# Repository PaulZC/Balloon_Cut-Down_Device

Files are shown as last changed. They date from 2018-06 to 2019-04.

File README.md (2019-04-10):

# Balloon_Cut-Down_Device

A cut-down device suitable for use on High Altitude Balloons and other remote actuation projects.



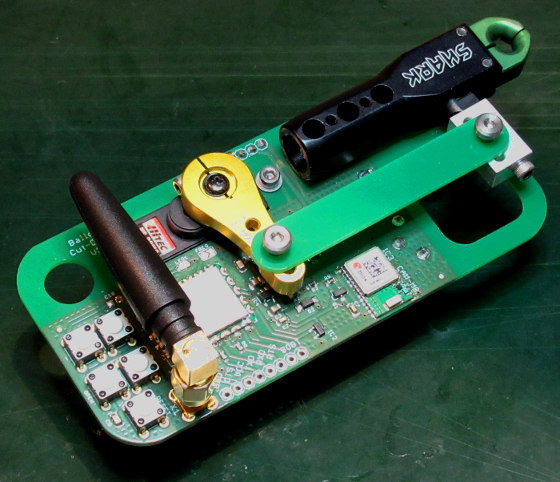
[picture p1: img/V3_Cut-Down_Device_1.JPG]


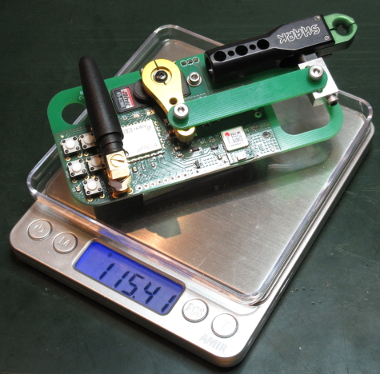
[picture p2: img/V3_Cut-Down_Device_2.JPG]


Designed to be triggered by the [Iridium Beacon Radio Board](https://github.com/PaulZC/Iridium_Beacon_Radio_Board),
carried by the [Iridium 9603N V5 Beacon](https://github.com/PaulZC/Iridium_9603_Beacon), the cut-down will be triggered
when it receives its own (unique) serial number on the chosen radio channel. The number of cut-downs that could be
triggered by a single Iridium Beacon is essentially unlimited. The cut-down can also be configured to trigger at
a pre-defined altitude.

The device comprises:
- [Scott Archery Shark release aid](https://scottarchery.com/collections/releases/products/shark-release), actuated by a
- [HiTec HS-82MG servo](https://www.servoshop.co.uk/index.php?pid=HITHS82MG&area=Servo), controlled by the
- [LPRS eRIC4 or eRIC9 integrated radio module](http://www.lprs.co.uk/products/easyradio-ism-modules/eric-soc-rf-modules.html).
- The altitude is provided by a [u-blox CAM-M8Q GNSS receiver](https://www.u-blox.com/en/product/cam-m8-series)

See [LEARN.md](https://github.com/PaulZC/Balloon_Cut-Down_Device/blob/master/LEARN.md) for further details.

See [SERVO.md](https://github.com/PaulZC/Balloon_Cut-Down_Device/blob/master/SERVO.md) for details on how to modify the HiTec servo for
high altitude operation.

See [SHARK.md](https://github.com/PaulZC/Balloon_Cut-Down_Device/blob/master/SHARK.md) for details on how to incorporate the Scott Archery Shark release aid
into the Cut-Down Device.

See [ASSEMBLY.md](https://github.com/PaulZC/Balloon_Cut-Down_Device/blob/master/ASSEMBLY.md) for details on how to assemble the PCB and the device itself.

See [CONFIGURE.md](https://github.com/PaulZC/Balloon_Cut-Down_Device/blob/master/CONFIGURE.md) for details on how to configure the servo positions and altitude limit.

See [Balloon_Cut-Down_Device.pdf](https://github.com/PaulZC/Balloon_Cut-Down_Device/blob/master/Balloon_Cut-Down_Device.pdf) for the schematic,
layout and Bill Of Materials.

The [Eagle](https://github.com/PaulZC/Balloon_Cut-Down_Device/tree/master/Eagle) directory contains the schematic and pcb design files.

The [eRIC](https://github.com/PaulZC/Balloon_Cut-Down_Device/tree/master/eRIC) directory contains the code for the eRIC integrated radio module.

The [Drawings](https://github.com/PaulZC/Balloon_Cut-Down_Device/tree/master/Drawings) directory contains the drawings for the trigger linkage.

If you have found this project useful and if you are able to, please cite the paper:

P. Clark et al, An open source toolkit for the tracking, termination and recovery of high altitude balloon flights and payloads, 2019 JINST 14 P04003
[DOI:10.1088/1748-0221/14/04/P04003](https://doi.org/10.1088/1748-0221/14/04/P04003)

The Accepted Manuscript is available on arXiv: http://arxiv.org/abs/1904.04321

This project is distributed under a Creative Commons Attribution + Share-alike (BY-SA) licence.
Please refer to section 5 of the licence for the "Disclaimer of Warranties and Limitation of Liability".

Enjoy!

**_Paul_**

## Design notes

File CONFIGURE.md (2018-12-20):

# Balloon Cut-Down Device - Configuration

A cut-down device suitable for use on High Altitude Balloons and other remote actuation projects.







Designed to be triggered by the [Iridium Beacon Radio Board](https://github.com/PaulZC/Iridium_Beacon_Radio_Board),
carried by the [Iridium 9603N V5 Beacon](https://github.com/PaulZC/Iridium_9603_Beacon), the cut-down will be triggered
when it receives its own (unique) serial number on the chosen radio channel. The number of cut-downs that could be
triggered by a single Iridium Beacon is essentially unlimited. The cut-down can also be configured to trigger at
a pre-defined altitude. The altitude is provided by a u-blox CAM-M8Q GNSS receiver.

## Set_Altitude:

There are two methods to set the altitude limit: using the switches; or via a radio message:

### Setting the Altitude Limit using the Switches:

The code enters Set_Altitude mode if the eRIC comes out of reset with the MINUS switch held down:
- Push and hold the MINUS switch;
- then press and release the RESET switch;
- then release the MINUS switch.
- The device will then enter Set_Altitude mode.



The LED will flash three times to show that the digit three is selected.

Pressing the MINUS switch decrements the digit by one.

Pressing the PLUS switch increments the digit by one.

Pressing the CLOSE switch causes the digit to be stored as the altitude limit tens of kilometers.

Pressing the OPEN switch causes the digit to be stored as the altitude limit units of kilometers.

In the animation, the sequence of events is:
- The MINUS switch is pressed and held
- The RESET switch is pressed and released
- The MINUS switch is released
- The cut-down is now in Set_Altitude mode
- The LED flashes three times to show the digit three
- The MINUS switch is pressed and released once
- The LED flashes twice to show the digit two
- The CLOSE switch is pressed and released
- Two is stored in the altitude limit tens of kilometers and the LED gives a long flash
- The MINUS switch is pressed and released once
- The LED flashes once to show the digit one
- The MINUS switch is pressed and released once
- The LED stops flashing to show the digit zero
- The OPEN switch is pressed and released
- Zero is stored in the altitude limit units of kilometers and the LED gives a long flash
- The altitude limit is now 20km
- The RESET switch is pressed and released
- The cut-down goes into normal operation
- The LED flashes twice, followed by a long flash, to indicate the altitude limit is 20km

The eRIC will stay in Set_Altitude mode until reset. Always reset the eRIC to start normal operation.

To disable the altitude limit, set it to 99km. This causes the CAM-M8Q GNSS receiver to be switched completely off,
significantly extending the battery life.

### Setting the Altitude Limit using a Radio Message:

Each eRIC has a unique serial number. The custom code running on the eRIC will set the altitude limit when it receives a data packet containing:
the eRIC serial number; followed by a "2"; followed by two digits which represent the altitude limit is kilometres.

If the serial number of the eRIC is _12345678_, an altitude limit of 33km (33000m) will be set when the eRIC receives:
- _12345678233_

If you are using the [Iridium Beacon](https://github.com/PaulZC/Iridium_9603_Beacon) and the
[Iridium Beacon Radio Board](https://github.com/PaulZC/Iridium_Beacon_Radio_Board) to control the cut-down, you will need to set the altitude limit via a RADIO command.

If you want to set the altitude limit to 33km (33000m), send:
- _[RADIO=12345678233]_

To set the altitude limit to 1km (1000m), send:
- _[RADIO=12345678201]_

The altitude limit can be disabled by setting it to 99km. This causes the CAM-M8Q GNSS receiver to be switched completely off, significantly extending the battery life.
Send:
- _[RADIO=12345678299]_

The altitude limit can be re-enabled by setting it to anything other than 99km.

## Set_Servo:

**It is safest to disconnect the trigger linkage from the servo arm _before_ putting the device into Set_Servo mode. Remove the shoulder screw which connects the
linkage to the servo arm. Replace it after the servo limits have been set and the device has been reset.**

**If you are setting the servo positions for the first time, do not install the servo arm on the servo until the device is in Set_Servo mode and the servo has moved to
its mid-range position.**

The code enters Set_Servo mode if the eRIC comes out of reset with the PLUS switch held down:
- Push and hold the PLUS switch;
- then press and release the RESET switch;
- then release the PLUS switch.
- The device will then enter Set_Servo mode.



The servo is moved to its mid-range position (PWM = 1500). 

Depending on whether the PLUS or MINUS switches are held down, the servo is moved towards one limit (PWM = 900) or the other (PWM = 2100).

With the Shark release closed, hold the trigger linkage over the servo arm and move the servo until the holes are slightly offset as shown.

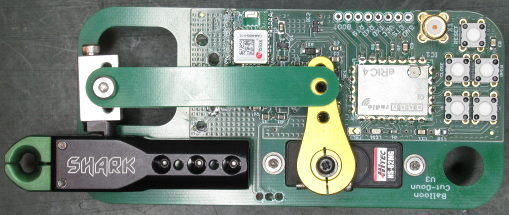
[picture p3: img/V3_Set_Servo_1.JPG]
V3_Set_Servo_1


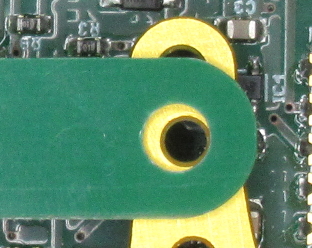
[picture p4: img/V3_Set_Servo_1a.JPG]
V3_Set_Servo_1a


When the CLOSE switch is pressed, the servo position is written into non-volatile memory. The LED will give a long flash while the setting is storted.

Next, open the Shark release and move the servo until the holes are slightly offset as shown.

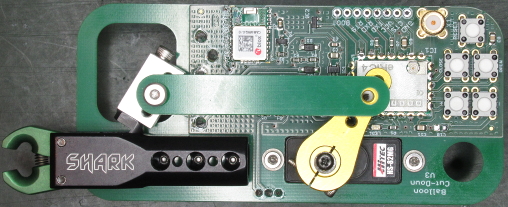
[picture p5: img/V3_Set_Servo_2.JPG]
V3_Set_Servo_2


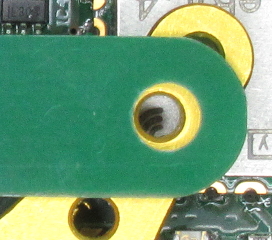
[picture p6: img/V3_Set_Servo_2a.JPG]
V3_Set_Servo_2a


When the OPEN switch is pressed, the servo position is written into non-volatile memory. The LED will give a long flash while the setting is storted.

It is important that the holes are slightly offset as shown, to prevent the servo from attempting to force the released aid open or closed.
This will damage the servo.

The eRIC will stay in this mode until reset.

As the servo is powered continuously in Set_Servo mode, the battery will discharge quickly if the device is left in this mode.
Always reset the device to put it back into Cut_Down mode when the servo positions have been stored.

After resetting the device, the shoulder screw can be replaced and the OPEN and CLOSE switches can be used to move the servo.

## Licence

This project is distributed under a Creative Commons Share-alike 4.0 licence.
Please refer to section 5 of the licence for the "Disclaimer of Warranties and Limitation of Liability".
  
Enjoy!

**_Paul_**

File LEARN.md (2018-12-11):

# Balloon Cut-Down Device

A cut-down device suitable for use on High Altitude Balloons and other remote actuation projects.







Designed to be triggered by the [Iridium Beacon Radio Board](https://github.com/PaulZC/Iridium_Beacon_Radio_Board),
carried by the [Iridium 9603N V5 Beacon](https://github.com/PaulZC/Iridium_9603_Beacon), the cut-down will be triggered
when it receives its own (unique) serial number on the chosen radio channel. The number of cut-downs that could be
triggered by a single Iridium Beacon is essentially unlimited. The cut-down can also be configured to trigger at
a pre-defined altitude. The altitude is provided by a u-blox CAM-M8Q GNSS receiver.

## The Design

See [Balloon_Cut-Down_Device.pdf](https://github.com/PaulZC/Balloon_Cut-Down_Device/blob/master/Balloon_Cut-Down_Device.pdf) for the schematic,
layout and Bill Of Materials.

The [Eagle](https://github.com/PaulZC/Balloon_Cut-Down_Device/tree/master/Eagle) directory contains the schematic and pcb design files.

See [ASSEMBLY.md](https://github.com/PaulZC/Balloon_Cut-Down_Device/blob/master/ASSEMBLY.md) for details on how to assemble the PCB and the device itself.

See [CONFIGURE.md](https://github.com/PaulZC/Balloon_Cut-Down_Device/blob/master/CONFIGURE.md) for details on how to configure the servo positions and altitude limit.

The key components of Balloon Cut-Down Device are:

### Scott Archery Shark Release Aid
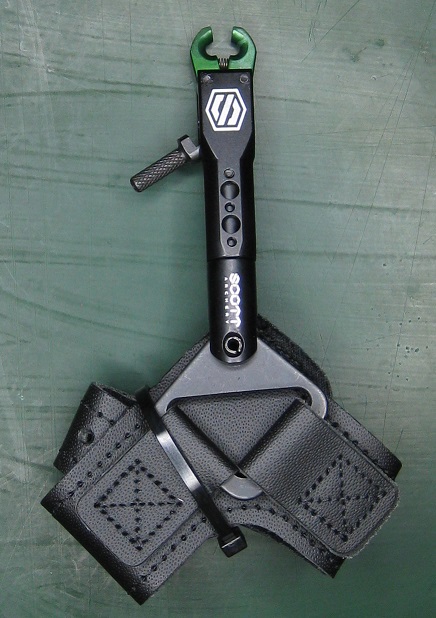
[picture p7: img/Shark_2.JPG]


- [Scott Archery Shark release aid](https://scottarchery.com/collections/releases/products/shark-release)

See [SHARK.md](https://github.com/PaulZC/Balloon_Cut-Down_Device/blob/master/SHARK.md) for details on how to incorporate the Scott Archery Shark release aid
into the Cut-Down Device.

### Hi-Tec HS-82MG Micro Servo
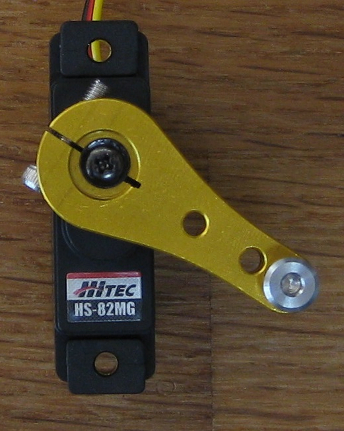
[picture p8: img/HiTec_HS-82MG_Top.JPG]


- [HiTec HS-82MG servo](https://www.servoshop.co.uk/index.php?pid=HITHS82MG&area=Servo)
- with [Tower Pro CH1.0H3G arm](https://www.servoshop.co.uk/index.php?pid=CH10H3G&area=ACCS)

See [SERVO.md](https://github.com/PaulZC/Balloon_Cut-Down_Device/blob/master/SERVO.md) for details on how to modify the HiTec servo for
high altitude operation.

### eRIC integrated controller
The heart of the Cut-Down Device is the eRIC4 or eRIC9 [easyRadio Integrated Controller](http://www.lprs.co.uk/products/easyradio-ism-modules/eric-soc-rf-modules.html).

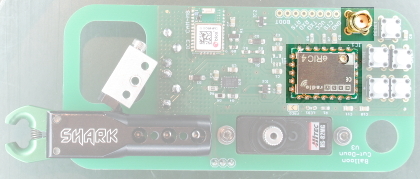
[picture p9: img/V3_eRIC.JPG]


Either an eRIC4 or an eRIC9 can be installed. The eRIC4 operates at 402-470 MHz for Europe, APAC and China. The eRIC9 operates at 804-940 MHz for Europe,
North & South America, India and China. Solder the _FREQ_ split pad to select the eRIC9 915 MHz band.

Each eRIC has a unique serial number. The custom code running on the eRIC will trigger the cut-down when it receives a data packet containing that serial number.

The Shark release will open when the eRIC receives:
- Its serial number
- Or its serial number followed by a "1"

The Shark release will close when the eRIC receives:
- Its serial number followed by a "0"

If the serial number of the eRIC is _12345678_, the Shark will open when the eRIC receives either:
- _12345678_

or
- _123456781_

The Shark will close when the eRIC receives:
- _123456780_

If you are using the [Iridium Beacon](https://github.com/PaulZC/Iridium_9603_Beacon) and the
[Iridium Beacon Radio Board](https://github.com/PaulZC/Iridium_Beacon_Radio_Board) to control the cut-down, you will need to send the commands:
- _[RADIO=12345678]_ or _[RADIO=123456781]_ to open the Shark release
- _[RADIO=123456780]_ to close the Shark release

You can set the altitude limit via radio by sending: the eRIC serial number; followed by a "2"; followed by two digits which represent the altitude limit is kilometres.

If you want to set the altitude limit to 33km (33000m), send:
- _[RADIO=12345678233]_

To set the altitude limit to 1km (1000m), send:
- _[RADIO=12345678201]_

The altitude limit can be disabled by setting it to 99km. This causes the CAM-M8Q GNSS receiver to be switched completely off, significantly extending the battery life.
Send:
- _[RADIO=12345678299]_

The altitude limit can be re-enabled by setting it to anything other than 99km.

### u-blox CAM-M8Q GNSS Receiver
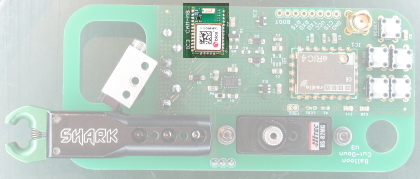
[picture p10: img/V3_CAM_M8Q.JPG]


Altitude data is provided by a u-blox CAM-M8Q GNSS receiver. To save power, the CAM-M8Q is configured to use only GPS satellites and ignores GLONASS, Galileo and BeiDou satellites.
Once the receiver has established a fix, the CAM-M8Q is put into low power mode to further extend the battery life. The CAM-M8Q can be disabled by setting the altitude limit to 99km.

### MCP111T-240 Reset Supervisor
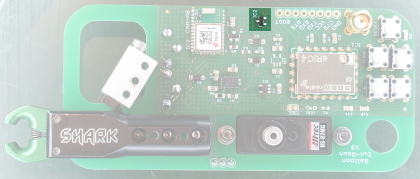
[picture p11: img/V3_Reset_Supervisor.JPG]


The Microchip MCP111-240 has an open drain output which holds the eRIC in reset until the supply rises above 2.4V, ensuring a clean start on power-up.

### SPX3819-3.3 Voltage Regulator
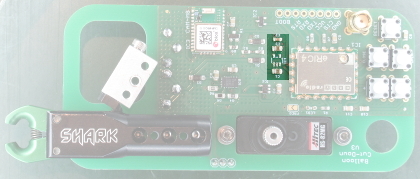
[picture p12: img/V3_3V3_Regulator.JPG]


The SPX3819-3.3 Voltage Regulator regulates the output from the battery, or the USB port, providing 3.3V for the eRIC and the CAM-M8Q.

MBR120 diodes protect the USB port and the battery from each other.

### MPM3610 Voltage Regulator
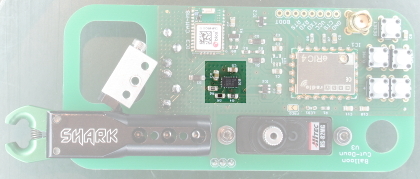
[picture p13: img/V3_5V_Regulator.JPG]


The MPM3610 Voltage Regulator regulates the output from the battery, providing 5V for the servo. The servo will only operate when a battery is connected, it
won't work when the device is powered from USB alone.

### 74AHCT1G125 Level Shifter
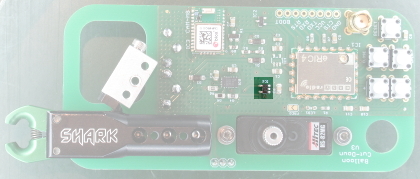
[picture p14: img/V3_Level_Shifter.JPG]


The 74AHCT1G125 Level Shifter is a non-inverting buffer which converts the 3.3V Pulse Width Modulation pulses from the eRIC to 5V for the servo.

### Switches
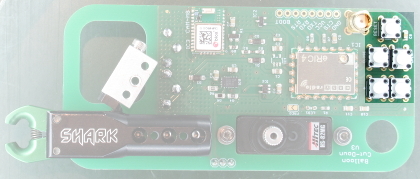
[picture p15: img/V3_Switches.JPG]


The cut-down device has five switches:
- CLOSE
- OPEN
- PLUS (+)
- MINUS (-)
- RESET

Press and release RESET to reset the eRIC.

Pressing OPEN will cause the servo to move the Shark trigger to the open position.

Pressing CLOSE will cause the servo to move the Shark trigger to the closed position.

The PLUS and MINUS switches are used to put the device into [Set_Servo](https://github.com/PaulZC/Balloon_Cut-Down_Device/blob/master/CONFIGURE.md#set_servo)
or [Set_Altitude](https://github.com/PaulZC/Balloon_Cut-Down_Device/blob/master/CONFIGURE.md#set_altitude) mode at reset.

### I/O Pins
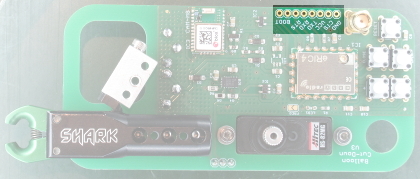
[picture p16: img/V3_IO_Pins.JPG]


The eight input/output pins are used to configure the eRIC. See [Configure the eRIC](https://github.com/PaulZC/Balloon_Cut-Down_Device/blob/master/ASSEMBLY.md#configure-the-eric)
for more details.

### Servo Pins
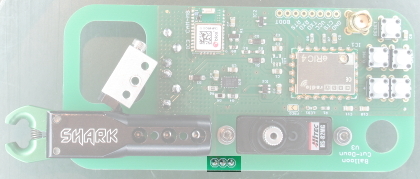
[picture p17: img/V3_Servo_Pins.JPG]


Connect the Hi-Tec HS-82MG Micro Servo to the PCB using standard 0.1" header strip (three-way) (e.g. Farnell 1593425)

## How much does the device weigh?

Including an Energiser® Ultimate Lithium L522 (PP3) battery, it weighs 115g.

V3_Cut-Down_Device_2

## What fasteners do I need?

To secure the servo to the base plate:
- M2.5 x 14 Hex Drive Screw x 2 (McMaster 91292A017)
- M2.5 Nylon-Insert Locknut x 2 (McMaster 93625A102)
- M2.5 Washer x 2 (McMaster 90965A115)

To secure the Shark release to the base plate:
- 4-40 UNC x ¼" Socket Head Screw x 3 (McMaster 92196A106)

To secure the trigger block to the Shark trigger:
- 4-40 UNC x ¾" Socket Head Screw (McMaster 92196A113)

To secure the trigger linkage to the trigger block and Tower Pro arm:
- M3 x 4mm Dia x 4mm Long Shoulder Screw x 2 (McMaster 90323A211)

## Antenna

Recommended antenna for the eRIC4 is:
- LPRS ANT-SR433 (Farnell part 2096221)

Recommended antenna for the eRIC9 is:
- LPRS ANT-SR900 (Farnell part 2096219)

http://www.lprs.co.uk/products/antennas-cables-connectors/stubby-antennas.html

The horizontal antenna orientation is important if the cut-down is positioned directly above the Iridium Beacon Radio Board on the balloon cord.

## Which 9V battery should I use?

Energiser® Ultimate Lithium L522 (PP3)

## Will this really work at altitude?

Yes. I have tested the device at -47C using dry ice. The servo moved slower than usual at that temperature, but it did release as expected.
The device was powered by an Energiser® Ultimate Lithium L522 (PP3) battery. A standard 9V battery won't work at that temperature.

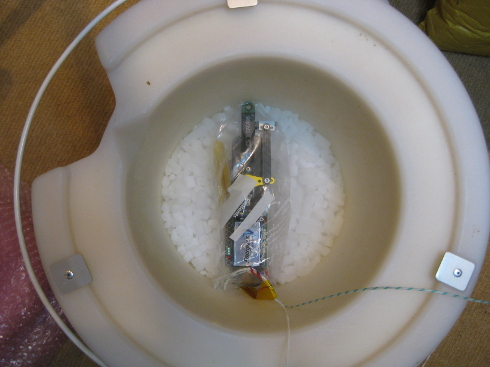
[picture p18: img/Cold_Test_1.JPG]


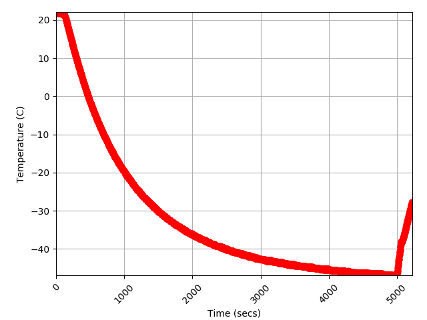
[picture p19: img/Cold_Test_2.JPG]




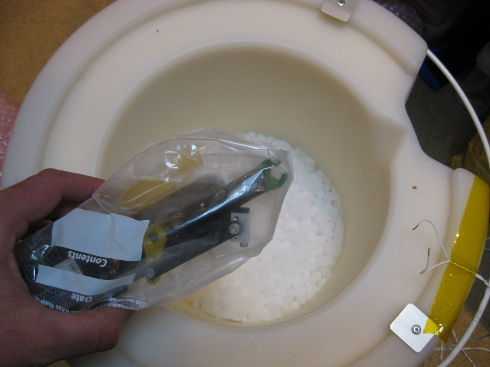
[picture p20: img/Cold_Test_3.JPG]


## Do you recommend coating the board once it is populated?

As a minimum, I'd recommend applying a coat of acrylic protective lacquer to the processor and surrounding components (especially the crystal).
If you're using an aerosol, be careful to mask off the connectors and switches first.

## How do I set the servo positions and altitude limit?

See [CONFIGURE.md](https://github.com/PaulZC/Balloon_Cut-Down_Device/blob/master/CONFIGURE.md) for details on how to configure the servo positions and altitude limit.

## The LED flashes when I connect the battery or reset the eRIC. Why?

When the battery is connected or the reset switch is pressed, the cut-down goes into normal operation. The LED flashes to indicate the altitude limit. The default is
33km so the LED will flash three times, pause, then flash three times again.

A zero is indicated by a long flash. Two flashes followed by a long flash indicates an altitude limit of 20km.
A long flash followed by one flash indicates a limit of 1km.

To test that the CAM-M8Q is operating correctly, try setting an altitude limit of 0km (indicated by two long flashes).
The Shark will open as soon as a GPS signal is acquired (unless you are below sea level!).

## Acknowledgements

This project wouldn't have been possible without the open source designs and code kindly provided by:

### LPRS
- http://www.lprs.co.uk/products/easyradio-ism-modules/eric-soc-rf-modules.html
- http://www.lprs.co.uk/assets/files/eRIC4_9_Datasheet_1.34.pdf
- http://www.lprs.co.uk/assets/files/Custom%20programming%20eRIC.zip
- http://www.lprs.co.uk/knowledge-centre/code-examples.html

### Alan Carvalho de Assis
- https://github.com/acassis/tinygps

### Mikal Hart
- https://github.com/mikalhart/TinyGPS

## Licence

This project is distributed under a Creative Commons Share-alike 4.0 licence.
Please refer to section 5 of the licence for the "Disclaimer of Warranties and Limitation of Liability".

Enjoy!

**_Paul_**

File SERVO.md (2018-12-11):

# Servo Modification

The Balloon Cut-Down Device uses a [HiTec HS-82MG servo](https://www.servoshop.co.uk/index.php?pid=HITHS82MG&area=Servo) to operate the
[Scott Archery Shark release aid](https://scottarchery.com/collections/releases/products/shark-release). These servos are lightweight and provide high torque
for their size. But, to allow them to operate reliably at high altitude (low pressure) and low temperature, the standard grease inside the servo needs to be
replaced and lacquer needs to be applied to the internal circuit board.

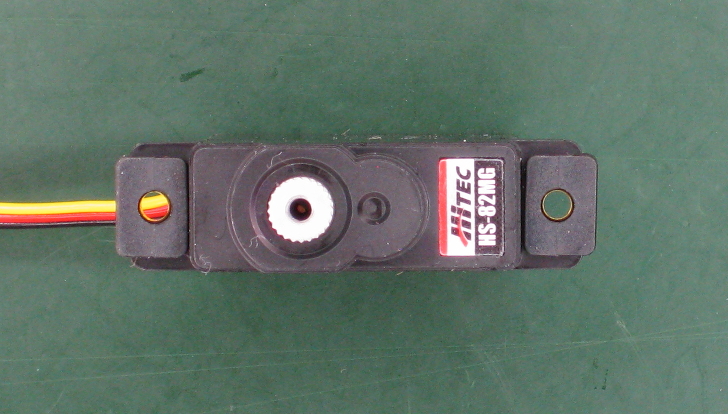
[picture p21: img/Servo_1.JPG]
Servo_1


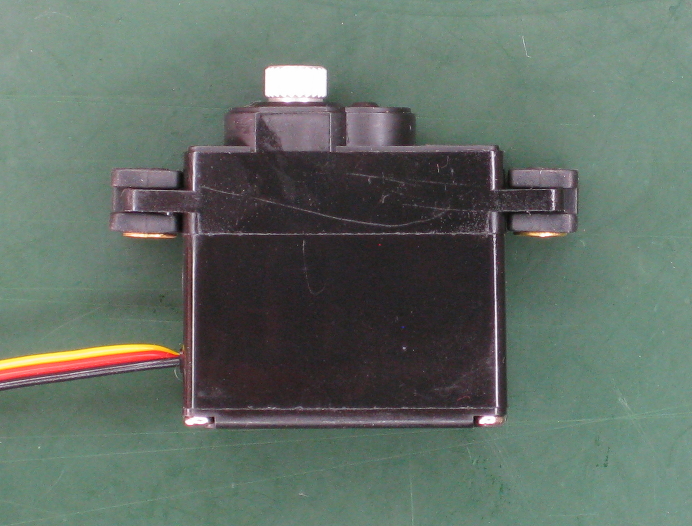
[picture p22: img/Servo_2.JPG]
Servo_2


### Set the Servo to Mid-Range

When you connect the servo to a freshly-programmed cut-down device circuit board and press either the Open or the Close button, the circuit board will
move the servo to its mid-range position. The servo position is set by a Pulse Width Modulation (PWM) signal on the yellow wire. A pulse width of 1.5msec
(1500usec) repeating every 20msec (50Hz) will set the servo to mid-range. It is important you do this as it will help you relocate the half-moon output gear
in the correct position.

You can see how the PWM pulse width causes the servo position to change in the following three images:

- Pulse Width 900usec (0.9msec)

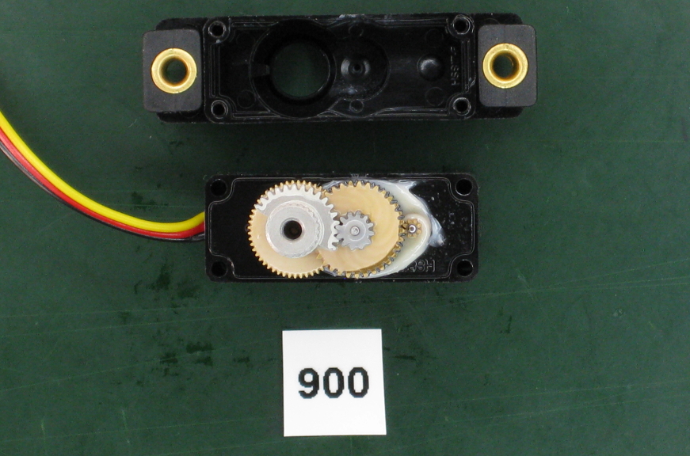
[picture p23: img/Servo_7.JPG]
Servo_7


- Pulse Width 1500usec (1.5msec)

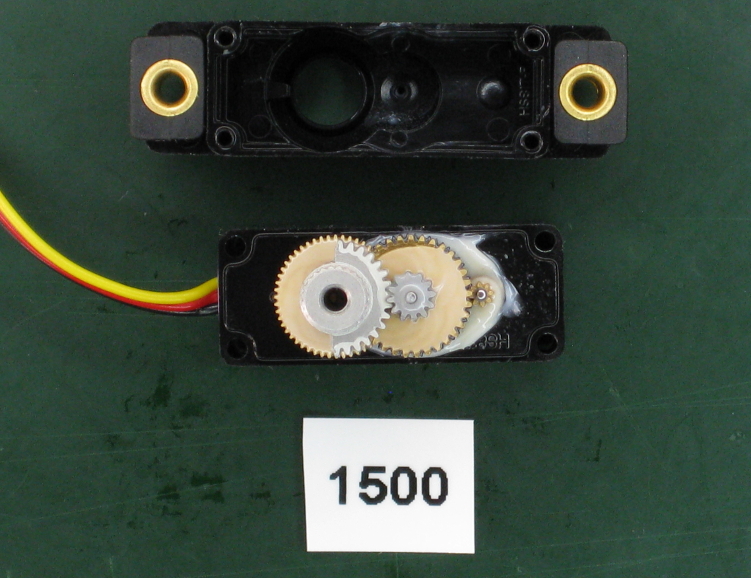
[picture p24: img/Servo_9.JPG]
Servo_9


- Pulse Width 2100usec (2.1msec)

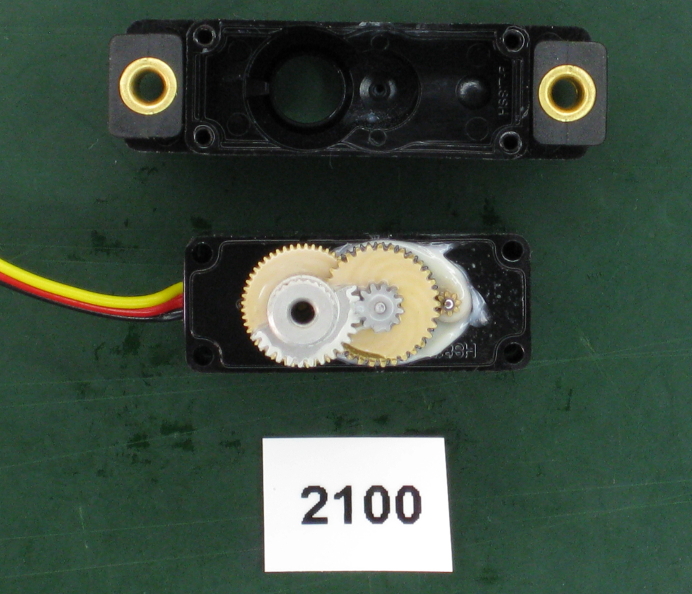
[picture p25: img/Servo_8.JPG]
Servo_8


### Remove the Screws

Remove the four screws which hold the servo case parts together. You will need a good quality Philips size OO screwdriver
such as the [Wiha PicoFinish 261 P 512](http://uk.farnell.com/wiha/2610040/screwdriver-phillips-no-00x40mm/dp/282303).

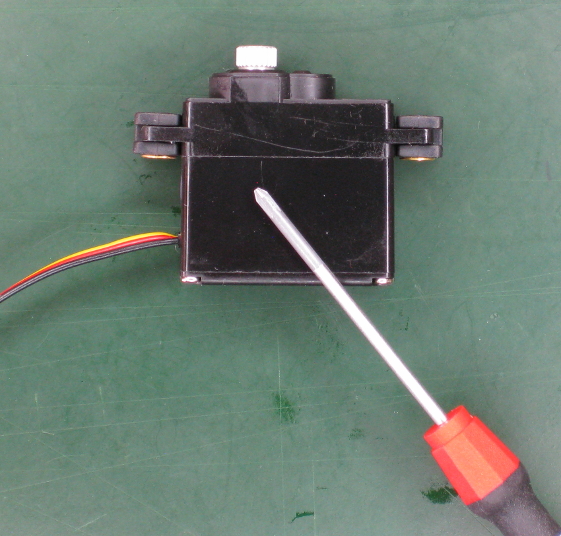
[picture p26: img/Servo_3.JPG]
Servo_3


Servo_4

### Remove the Standard Grease

Using several [cotton-buds, Q-tips or swabs](https://www.thorlabs.de/thorproduct.cfm?partnumber=CTA10), remove the standard grease from the top part
of the servo housing. Be careful not to leave any cotton strands behind.

Servo_5

Servo_6

Carefully remove the four gears, one at at time, and wipe the grease from each of them using [lint-free lens tissue](https://www.thorlabs.de/thorproduct.cfm?partnumber=MC-5).

Servo_10

### Observe the Output Shaft Position

Once the grease is removed, you will be able to observe the flat on the output shaft. The half-moon output gear has a matching flat to locate it
precisely on the shaft.

Servo_11

### Servo Electronics

Take a look at the servo electronics: PCB with driver IC and push-pull transistors; output shaft position-sensing potentiometer; and DC motor. I do recommend
giving both sides of the driver PCB a coat of lacquer, especially if you are intending to use it at altitude. Cover all of the PCB components with a layer of
[Acrylic Protective Lacquer (conformal coating)](https://uk.rs-online.com/web/p/conformal-coatings/3217324/) between and around the glue HiTec have applied
to the servo wiring. Let the coating dry before you reassemble the servo.

Servo_12

Servo_13

Servo_13a

The servo works by responding to the incoming PWM signal. The motor is driven in one direction or the other by the push-pull driver, until the potentiometer
senses that the output shaft is in the desired position.

### Apply Space Grease

Apply a little Castrol Braycote 601 EF grease to the teeth on all four gears plus the small gear on the motor shaft. Braycote 601 EF is a low temperature (-80C),
low outgassing, non-flammable, non-toxic grease which is approved by NASA. It is expensive, but you are only going to use a very small amount modifying each servo.

Servo_14

### Reassemble

Reassemble the four gears onto the two shafts taking care to match the half-moon output gear with the flat on the output shaft.

Close the case and reinsert the four screws. Do not over-tighten the screws. Label the servo to indicate that the grease has been replaced.

Servo_15

### Shorten the Cable

If you have suitable crimps and a crimp tool available, it is advantageous to shorten the servo cable.

Servo_16

Servo_17

Modifying the servo will of course void your warranty.

This project is distributed under a Creative Commons Attribution + Share-alike (BY-SA) licence.
Please refer to section 5 of the licence for the "Disclaimer of Warranties and Limitation of Liability".

Enjoy!

**_Paul_**

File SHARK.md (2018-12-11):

# Shark Release Aid Modification

The Balloon Cut-Down Device uses a [HiTec HS-82MG servo](https://www.servoshop.co.uk/index.php?pid=HITHS82MG&area=Servo) to operate the
[Scott Archery Shark release aid](https://scottarchery.com/collections/releases/products/shark-release). The Shark is a well designed piece
of kit, able to withstand high release loads and yet operate with the minimum of trigger pressure.

Shark_1

Shark_2

### Remove the Wrist Strap

Use a 3/32" hexagon key to remove the 4-40 screw which secures the Shark release to the swivel.

Shark_3

### Versions

The Shark release comes in two versions: one with a removeable trigger and one with a fixed, one-piece trigger. Choose the corresponding
trigger block to match whichever version you have: one replaces the removeable trigger; one slides over the fixed trigger.

Shark_4

### Apply Space Grease

It may be overkill, but I would recommend replacing the standard machine oil in the release with Castrol Braycote 601 EF grease. Braycote 601 EF is a
low temperature (-80C), low outgassing, non-flammable, non-toxic grease which is approved by NASA. It is expensive, but you are only going to need a
very small amount to modify each release.

Shark_5

Working from the side of the release that has the Scott logo (not the word "Shark"), use a 1.6mm parallel pin punch to tap out the pin holding the
jaw nearest the trigger in place.

The two jaws are pushed apart by a spring. Hold them together as you remove the pin, otherwise the spring will disappear into the darkest corner of
your workshop! There is also a ball bearing which makes the jaws move together. Be careful this doesn't also roll away into that same dark corner.

Wipe off the machine oil and then apply Braycote sparingly to all the moving parts.

Re-insert the pin and tap it back into place, working from the side of the release with the word "Shark" on it.

### Add the Trigger Block

[Cut-Down_Device.pdf](https://github.com/PaulZC/Balloon_Cut-Down_Device/blob/master/Drawings/Cut-Down_Device.pdf) contains the drawings for the two
different versions of the trigger block.

- If your Shark has a green anodised removeable trigger, unscrew it and install the first version of the trigger block using a 3/4" 4-40 UNC screw.
- If your Shark has a black fixed trigger, slide the second version of the trigger block over the trigger using a small amount of epoxy to secure it in place.

Modifying the Shark will of course void your warranty.

This project is distributed under a Creative Commons Attribution + Share-alike (BY-SA) licence.
Please refer to section 5 of the licence for the "Disclaimer of Warranties and Limitation of Liability".

Enjoy!

**_Paul_**

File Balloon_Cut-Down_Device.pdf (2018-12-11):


thunderbird\hom e\pclark\D ocum ents\eagle\Balloon_C ut-D ow n\Balloon_C ut-D ow n_V3\Balloon_C ut-D ow n.sch (Sheet: 1/2)


thunderbird\hom e\pclark\D ocum ents\eagle\Balloon_C ut-D ow n\Balloon_C ut-D ow n_V3\Balloon_C ut-D ow n.sch (Sheet: 2/2)


05/11/2018 15:00 \\thunderbird\hom e\pclark\D ocum ents\eagle\Balloon_C ut-D ow n\Balloon_C ut-D ow n_V3\Balloon_C ut-D ow n.brd



Part X | Y | Angle Package Value | Manufacturer | Manufacturer Part No

Farnell
Part No

RS Part
No | Mouser Part No | Description

Fiducials - for solder paste mask alignment:

FD1 | 34.89 | 3.18 | | | | | | Fiducial 1mm
FD2 | 64.10 77.47 | Fiducial 1mm

Surface Mount Components:

C1 | 46.1 43.08 | 270 0805 | 10µF | Walsin | 0805F106Z100CT | 2496998 | MultiLayer Ceramic Capacitor; 10uF; 10V; 0805
C2 | 53.18 43.15 | 270 0805 | 10µF | Walsin | 0805F106Z100CT | 2496998 | MultiLayer Ceramic Capacitor; 10uF; 10V; 0805
C3 | 56.01 43.12 | 270 0603 | 0.1uF | Murata | GRM188R71H104JA93D 2688523 | MultiLayer Ceramic Capacitor; 0.1uF; 50V; 0603; X7R
C4 | 44.64 62.04 | 0 0805 | 10µF | Walsin | 0805F106Z100CT | 2496998 | MultiLayer Ceramic Capacitor; 10uF; 10V; 0805
C5 | 46.42 | 56.9 | 90 0805 | 10µF | Walsin | 0805F106Z100CT | 2496998 | MultiLayer Ceramic Capacitor; 10uF; 10V; 0805
C6 | 40.7 42.48 | 0 0805 | 10nF | Walsin | 0805B103K500CT | 2496939 | MultiLayer Ceramic Capacitor; 10nF; 50V; 0805; X7R
C7 | 61.18 57.12 | 0 0805 | 0.1uF | Walsin | 0805B104K500CT | 2496944 | MultiLayer Ceramic Capacitor; 0.1uF; 50V; 0805; X7R
C8 | 57.82 | 3.18 | 180 0805 | 10nF | Walsin | 0805B103K500CT | 2496939 | MultiLayer Ceramic Capacitor; 10nF; 50V; 0805; X7R
C9 | 56.55 | 25.4 | 180 0805 | 10nF | Walsin | 0805B103K500CT | 2496939 | MultiLayer Ceramic Capacitor; 10nF; 50V; 0805; X7R
C10 | 34.93 15.91 | 270 0805 | 1nF | Walsin | 0805B102J500CT | 2496932 | MultiLayer Ceramic Capacitor; 1nF; 50V; 0805; X7R
C11 | 34.93 20.92 | 90 0805 | 10nF | Walsin | 0805B103K500CT | 2496939 | MultiLayer Ceramic Capacitor; 10nF; 50V; 0805; X7R
D1 | 49.43 49.56 | 90 SOD-123 MBR120 | ON SEMICONDUCTOR MBR120VLSFT1G | 1431044 | Schottky Rectifier; 20V; 1A; SOD-123
D2 | 55.25 49.53 | 90 SOD-123 MBR120 | ON SEMICONDUCTOR MBR120VLSFT1G | 1431044 | Schottky Rectifier; 20V; 1A; SOD-123
D3 | 43.82 67.95 | 90 SOD-123 MBR120 | ON SEMICONDUCTOR MBR120VLSFT1G | 1431044 | Schottky Rectifier; 20V; 1A; SOD-123
IC1 | 45.72 28.58 | 90 | ERIC4 | LPRS | ERIC4 | 2362439 | LPRS easy Radio Intelligent Controller 433MHz
| | | | ERIC9 | LPRS | ERIC9 | 2362440 | LPRS easy Radio Intelligent Controller 868/915MHz
IC2 | 61.6 48.26 | 0 SOT23-3 MCP111T-240E/TT Microchip | MCP111T-240E/TT | 1627192 | Reset Supervisor; SOT23-3; 2.40V; Open Drain; Active Low
IC3 | 58.1 64.77 | 0 | CAM-M8Q | u-blox | CAM-M8Q | https://www.u-blox.com/en/product/cam-m8-series
IC4 | 49.56 43.21 | 270 SOT23-5 SPX3819-3.3 | Exar | SPX3819M5-L-3-3/TR | 701-SPX3819M5-L-33TR LDO Voltage Regulator; 500mA; SOT-23-5
IC5 | 42.58 57.96 | 0 QFN-20 MPM3610 | MPS | MPM3610AGQV-P | 946-MPM3610AGQV-P Switching Voltage Regulator; 21V; 1.2A; DC/DC
IC6 | 40.64 46.96 | 0 SOT23-5 74AHCT1G125DBV Texas Instruments | SN74AHCT1G125DBVR | 1105927 | Buffer / Line Driver; Single Gate
LED1 | 34.93 32.38 | 0 2.0x1.25 RED | Wurth Electronik | 150080RS75000 | 2322077 | 710-150080RS75000 | LED; Red; 20mA; 2V; 2.0x1.25mm
Q1 | 56.8 56.64 | 270 SOT23 | DMG3415U-7 | Diodes Inc. | DMG3415U-7 | 1843688 | MOSFET; P Channel; SOT23-WIDE
R1 | 34.89 27.94 | 90 0603 | 1K | Multicomp | MCWR06X1001FTL | 2447272 | Chip Resistor; Thick Film; 1k; 50V; 0603; 100mW
R2 | 52.04 48.58 | 270 0603 | 330K | Multicomp | MCWR06X3303FTL | 2447338 | Resistor, Thick Film, 330K, 1%, 50V, 100mW, 0603
R3 | 52.01 | 52.9 | 270 0603 | 100K | Multicomp | MC01W08051100K | 9332405 | Chip Resistor; Thick Film; 100k; 150V; 0805; 100mW
R4 | 38.32 56.77 | 270 0805 | 100K_1% | Panasonic | ERJ6ENF1003V | 2303757 | Resistor, Thick Film, 100K, 1% 0.125W, 0805
R5 | 38.32 60.77 | 270 0805 | 19K1_0.1% | Panasonic | ERA6ARB1912V | 2094729 | Resistor, Thin Film, 19K1, 0.1%, 0.125W, 0805
R6 | 40.61 62.99 | 270 0805 | 68k | Multicomp | MCWR08X6802FTL | 2447706 | Resistor, Thick Film, 68K, 1%, 0.125W
R7 | 56.52 28.58 | 180 0603 | 1K | Multicomp | MCWR06X1001FTL | 2447272 | Chip Resistor; Thick Film; 1k; 50V; 0603; 100mW
R8 | 56.52 32.38 | 180 0603 | 1K | Multicomp | MCWR06X1001FTL | 2447272 | Chip Resistor; Thick Film; 1k; 50V; 0603; 100mW
R9 | 53.4 56.71 | 90 0603 | 100K | Multicomp | MC01W08051100K | 9332405 | Chip Resistor; Thick Film; 100k; 150V; 0805; 100mW

Non-surface mount components:

BAT | | | | | Keystone | 593 + 594 | 723988 | Battery Contact, PP3 (9V), Snap Contact, Steel, Nickel Plated
X1 | IMS | 42.2510.009 | 112-3794 | Straight 50Ω Through Hole SMA Connector
S1 | | | | | Multicomp | MCDTS6-1N | 9471685 | Switch, SPST, 0.05A, 12VDC, 160gf
S2 | | | | | Multicomp | MCDTS6-1N | 9471685 | Switch, SPST, 0.05A, 12VDC, 160gf
S3 | | | | | Multicomp | MCDTS6-1N | 9471685 | Switch, SPST, 0.05A, 12VDC, 160gf
S4 | | | | | Multicomp | MCDTS6-1N | 9471685 | Switch, SPST, 0.05A, 12VDC, 160gf
S5 | | | | | Multicomp | MCDTS6-1N | 9471685 | Switch, SPST, 0.05A, 12VDC, 160gf

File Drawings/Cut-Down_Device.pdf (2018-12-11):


Scott Archery
Shark
Release Aid

(Left: Fixed Trigger Right: Removable Trigger) 61.2 49.5


12.9

6.5

6.4

9.7

Trigger Block for Removable Trigger Version; M3.0 Tap Thro’ Three Places

Aluminium Plate
Thickness: ¼”

Secured with
McMaster
92196A113
4-40 UNC x ¾” Screw

M3.0 Tap Thro’ Three Places

Trigger Block
for Fixed Trigger Version

Aluminium Plate
Thickness: ¼”

Secured with
Epoxy


HiTec HS-82MG
with
Tower Pro
CH1.0H3G arm
and
McMaster
90323A211
shoulder screw

11.9

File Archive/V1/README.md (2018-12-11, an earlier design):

# Balloon_Cut-Down_Device

A cut-down device suitable for use on High Altitude Balloons and other remote actuation projects.







Designed to be interfaced to the [Iridium 9603N V5 Beacon](https://github.com/PaulZC/Iridium_9603_Beacon), but can be operated by: any push-to-close
switch; a normally-open relay contact; or a 3.3V logic signal.

The device comprises:
- [Scott Archery Shark release aid](https://scottarchery.com/collections/releases/products/shark-release), actuated by a
- [HiTec HS-82MG servo](https://www.servoshop.co.uk/index.php?pid=HITHS82MG&area=Servo), controlled by
- Arduino-compatible electronics based on the Adafruit Adalogger Feather M0, incorporating the Atmel SAMD21G18A processor, mounted on a
- bespoke carbon-fibre base plate with carbon-fibre linkage between the servo and the release aid

See [LEARN.md](https://github.com/PaulZC/Balloon_Cut-Down_Device/blob/master/Archive/V1/LEARN.md) for further details.

See [SERVO.md](https://github.com/PaulZC/Balloon_Cut-Down_Device/blob/master/Archive/V1/SERVO.md) for details on how to modify the HiTec servo for
high altitude operation.

See [SHARK.md](https://github.com/PaulZC/Balloon_Cut-Down_Device/blob/master/Archive/V1/SHARK.md) for details on how to incorporate the Scott Archery Shark release aid
into the Cut-Down Device.

See [ASSEMBLY.md](https://github.com/PaulZC/Balloon_Cut-Down_Device/blob/master/Archive/V1/ASSEMBLY.md) for details on how to assemble the PCB and the device itself.

See [Balloon_Cut-Down_Device.pdf](https://github.com/PaulZC/Balloon_Cut-Down_Device/blob/master/Archive/V1/Balloon_Cut-Down_Device.pdf) for the schematic,
layout and Bill Of Materials.

The [Eagle](https://github.com/PaulZC/Balloon_Cut-Down_Device/tree/master/Archive/V1/Eagle) directory contains the schematic and pcb design files.

The [Arduino](https://github.com/PaulZC/Balloon_Cut-Down_Device/tree/master/Archive/V1/Arduino) directory contains the Arduino code.

The [Drawings](https://github.com/PaulZC/Balloon_Cut-Down_Device/tree/master/Archive/V1/Drawings) directory contains the drawings for the carbon-fibre base plate
and trigger linkage.

Enjoy!

**_Paul_**

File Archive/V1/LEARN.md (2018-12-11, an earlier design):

# Balloon Cut-Down Device

A cut-down device suitable for use on High Altitude Balloons and other remote actuation projects.







Designed to be interfaced to the [Iridium 9603N V5 Beacon](https://github.com/PaulZC/Iridium_9603_Beacon), but can be operated by: any push-to-close
switch; normally-open relay contact; or a 3.3V logic signal.

## Background

The cut-down device is designed to release the payload from a high altitude balloon. When connected to an
[Iridium 9603N Beacon](https://github.com/PaulZC/Iridium_9603_Beacon) it can be actuated from the ground via an Iridium Short Burst Data message.
However, the device could also operate stand-alone when connected to: an external GNSS (GPS) receiver via the Serial1 pins; or an external
altitude sensor via the I2C pins.

The device has been designed such that multiple devices can be connected together in parallel, using one pair of wires, and triggered
consecutively by increasing trigger pulse widths. When connected in parallel, make sure the GND pins on each device are linked together.





## The Design

See [Balloon_Cut-Down_Device.pdf](https://github.com/PaulZC/Balloon_Cut-Down_Device/blob/master/Archive/V1/Balloon_Cut-Down_Device.pdf) for the schematic,
layout and Bill Of Materials.

The [Eagle](https://github.com/PaulZC/Balloon_Cut-Down_Device/tree/master/Archive/V1/Eagle) directory contains the schematic and pcb design files.

See [ASSEMBLY.md](https://github.com/PaulZC/Balloon_Cut-Down_Device/blob/master/Archive/V1/ASSEMBLY.md) for details on how to assemble the PCB and the device itself.

The key components of Balloon Cut-Down Device are:

### Scott Archery Shark Release Aid


- [Scott Archery Shark release aid](https://scottarchery.com/collections/releases/products/shark-release)

See [SHARK.md](https://github.com/PaulZC/Balloon_Cut-Down_Device/blob/master/Archive/V1/SHARK.md) for details on how to incorporate the Scott Archery Shark release aid
into the Cut-Down Device.

### Hi-Tec HS-82MG Micro Servo


- [HiTec HS-82MG servo](https://www.servoshop.co.uk/index.php?pid=HITHS82MG&area=Servo)
- with [Tower Pro CH1.0H3G arm](https://www.servoshop.co.uk/index.php?pid=CH10H3G&area=ACCS)

See [SERVO.md](https://github.com/PaulZC/Balloon_Cut-Down_Device/blob/master/Archive/V1/SERVO.md) for details on how to modify the HiTec servo for
high altitude operation.

### Carbon-Fibre Parts

The [Drawings](https://github.com/PaulZC/Balloon_Cut-Down_Device/tree/master/Archive/V1/Drawings) directory contains the drawings for the carbon-fibre base plate
and trigger linkage.

Assembly_14

### The PCB

[ASSEMBLY.md](https://github.com/PaulZC/Balloon_Cut-Down_Device/tree/master/Archive/V1/ASSEMBLY.md) contains full instructions for the assembly of the PCB and
the Cut-Down Device itself.

Assembly_13

### Atmel ATSAMD21G18 Processor


As used on the Adafruit Feather M0:
- https://www.adafruit.com/products/2772

### MCP111T-240 Reset Supervisor


The Microchip MCP111-240 has an open drain output which holds the processor in reset until the supply rises above 2.4V, ensuring a clean start on power-up.

### SPX3819-3.3 Voltage Regulator


The SPX3819-3.3 Voltage Regulator regulates the output from the battery, or the USB port, providing 3.3V for the processor.

MBR120 diodes protect the USB port and the battery from each other.

### MPM3610 Voltage Regulator


The MPM3610 Voltage Regulator regulates the output from the battery, providing 5V for the servo. The servo will only operate when a battery is connected, it
won't work when the device is powered from USB alone.

### 74AHCT1G125 Level Shifter


The 74AHCT1G125 Level Shifter is a non-inverting buffer which converts the 3.3V Pulse Width Modulation pulses from the SAMD M0 processor to 5V for the servo.

### Switches


The cut-down device has five switches:
- CLOSE
- OPEN
- PLUS (+)
- MINUS (-)
- RESET

Press and release RESET to reset the processor. Pressing RESET twice quickly will put the processor into bootloader mode. The LED will fade up and down when in this
mode. Press RESET once to bring the processor back out of bootloader mode.

Pressing OPEN will cause the servo to move the Shark trigger to the open position.

Pressing CLOSE will cause the servo to move the Shark trigger to the closed position.

The PLUS and MINUS switches are used to put the device into [Set_Servo](https://github.com/PaulZC/Balloon_Cut-Down_Device/blob/master/Archive/V1/LEARN.md#set_servo)
or [Set_Duration](https://github.com/PaulZC/Balloon_Cut-Down_Device/blob/master/Archive/V1/LEARN.md#set_duration) mode.

## IO Pins


**OPEN** and **CLOSE** can be used to open and close the Shark release via the servo. The OPEN and CLOSE push switches are connected to the same pins.
Pull OPEN low, through a push-to-close switch or a normally-open relay contact, to trigger the cut-down device.

To connect the cut-down device to an [Iridium 9603N V5 Beacon](https://github.com/PaulZC/Iridium_9603_Beacon), connect **GND** and **OPEN** to the beacon relay **COM** and **NO** pins using twin core cable.
If a Mobile Terminated message is sent to the beacon containing the text _[RELAY=1]_ , the relay NO contact will pulse closed for 1 second.
This will trigger the device if intDuration is set to '0' or '1' (see [Set_Duration](https://github.com/PaulZC/Balloon_Cut-Down_Device/blob/master/Archive/V1/LEARN.md#set_duration)).

OPEN and CLOSE are connected to 3.3V inputs with pull-ups on the SAMD M0 processor. Do not connect these pins to a 5V device directly - there is no additional over-voltage protection on these pins.
Use an open-collector transistor as a buffer if you do want to connect to a 5V device.



**SWCLK** and **SWDIO** are used during [programming of the SAMD bootloader](https://github.com/PaulZC/Balloon_Cut-Down_Device/blob/master/Archive/V1/LEARN.md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).

**RST** is the processor reset signal. Pull low to reset the processor.

**3V3** is the 3.3V power rail from the SPX3819-3.3 voltage regulator.
Any peripherals connected to this will be powered continuously when power is available from the battery or USB.

**VBUS** is the power bus connecting the battery and USB power rails. VBUS will be close to 5V when connected to USB alone, or close to 9V when the
battery is connected. This pin can be used to power the board during [programming of the SAMD bootloader](https://github.com/PaulZC/Balloon_Cut-Down_Device/blob/master/Archive/V1/LEARN.md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).



**3V3SW** is the 3.3V power rail switched by Q1 and which can provide power for external serial and I2C devices.
Use these pins to power peripherals which you want to be able to disable.

**SDA** and **SCL** are the I2C bus data and clock signals.
You could use these to connect an external I2C sensor - e.g. an MPL3115A2 altitude sensor.

**TX** and **RX** are the Serial1 transmit and receive pins. You could use these to connect to an external 3.3V GNSS (GPS) receiver.



**GND** and **5V** provide power for the servo. **PWM** is the 5V Pulse Width Modulated signal which sets the servo position.

When connecting the servo, ensure the black wire goes to GND, the red wire to 5V and the yellow wire to PWM.

## How much does the device weigh?
Including an Energiser® Ultimate Lithium L522 (PP3) battery, it weighs 135g.



The weight breaks down as follows:
- Battery (Energiser L522) 			33.9g
- PCB + Battery Holder				20.6g
- Shark Release (No Trigger) 			20.2g
- HS-82MG Servo 				19.8g
- Base Plate 					19.3g
- M3 x 16 Screws, Nuts, Spacers (4)		5.8g
- Tower Pro Arm 				4.4g
- Trigger Block 				2.2g
- Trigger Linkage 				2.2g
- M3 x 4 Shoulder Screws (2) 			1.8g
- M2.5 x 14 Screws, Nuts (2) 			2.1g
- 4-40 x ¼" Screws (3)				1.5g
- 4-40 x ¾" Screw 				1.0g

## What fasteners do I need?
To secure the PCB and battery holder to the base plate:
- M3 x 16 Hex Drive Screw x 4 (McMaster 92095A184)
- 4.5mm OD, 5mm Long Spacer x 4 (McMaster 94669A099)
- M3 Nylon-Insert Locknut x 4 (McMaster 93625A100)
- M3 Washer x 4 (McMaster 90965A130)

**You will need to file the top off the M3 button head screws to allow the battery to sit correctly in the battery holder.**

To secure the servo to the base plate:
- M2.5 x 14 Hex Drive Screw x 2 (McMaster 91292A017)
- M2.5 Nylon-Insert Locknut x 2 (McMaster 93625A102)
- M2.5 Washer x 2 (McMaster 90965A115)

To secure the Shark release to the base plate:
- 4-40 UNC x ¼" Socket Head Screw x 3 (McMaster 92196A106)

To secure the trigger block to the Shark trigger:
- 4-40 UNC x ¾" Socket Head Screw (McMaster 92196A113)

To secure the trigger linkage to the trigger block and Tower Pro arm:
- M3 x 4mm Dia x 4mm Long Shoulder Screw x 2 (McMaster 90323A211)

## Will this really work at altitude?

Yes. I have tested the device at -47C using dry ice. The servo moved slower than usual at that temperature, but it did release as expected.
The device was powered by an Energiser® Ultimate Lithium L522 (PP3) battery. A standard 9V battery won't work at that temperature.









## Have you performed a load test?

Yes. The device has been subjected to a Lead Brick Test. A 7kg lead brick was attached and released from the device 100 times. No problems
were observed!



## Do you recommend coating the board once it is populated?
As a minimum, I'd recommend applying a coat of acrylic protective lacquer to the processor and surrounding components (especially the crystal).
If you're using an aerosol, be careful to mask off the connectors and switches first.

## Arduino Code
The [Arduino](https://github.com/PaulZC/Balloon_Cut-Down_Device/tree/master/Archive/V1/Arduino) directory contains the Arduino code.

The main loop is structured around a switch / case statement which provides the three modes of operation:

### Cut_Down:
The SAMD M0 processor is woken up from deep sleep by an interrupt from the OPEN or CLOSE switch. It waits to see if the switch pin stays
low for the required amount of time (intDuration) then moves the servo to the open or closed position as appropriate.
By default, intDuration will be zero - i.e. the servo will move immediately. The M0 goes back into deep sleep when the
servo move is complete.



In reality, the required intDuration is decreased by 0.1 seconds to allow exact whole second key presses
to trigger the device. E.g. if intDuration is set to '1', a key press of 0.9s or longer will trigger the device.
This keeps things simple when triggering the device from an Iridium Beacon via Mobile Terminated messaging.

The LED will light up while the servo is moving. If the battery is low, the LED will flash quickly.

The servo will only operate when a battery is connected, it won't work when the device is powered from USB alone.

The cut-down device spends most of its time in deep sleep, which means that the Arduino IDE won't recognise it as connected. If you want to reprogram
the board, either:

- press the reset button twice quickly, to put the processor into bootloader mode

or:

- press and hold down the PLUS or MINUS switch, then press the reset switch briefly. Release the PLUS or MINUS switch after the LED goes out. This puts the
board into Set_Servo mode or Set_Duration mode where the processor is powered up continuously.

The Arduino IDE will then be able to connect to the board.

### Set_Servo:
**It is safest to disconnect the trigger linkage from the servo arm _before_ putting the device into Set_Servo mode. Remove the shoulder screw which connects the
linkage to the servo arm. Replace it after the servo limits have been set and the device has been reset into Cut_Down mode.**

**If you are setting the servo positions for the first time, do not install the servo arm on the servo until the device is in Set_Servo mode and the servo has moved to
its mid-range posiiton.**

The code enters Set_Servo mode if the M0 comes out of reset with the PLUS switch held down. Push and hold the PLUS switch, then press and release the RESET switch.
Keep PLUS pressed until the LED has come on and gone out. The device will then enter Set_Servo mode.



The servo is moved to its mid-range position (PWM = 1500). 

Depending on whether the PLUS or MINUS switches are held down, the servo is moved towards one limit (PWM = 900) or the other (PWM = 2100).



With the Shark release closed, hold the trigger linkage over the servo arm and move the servo until the holes are slightly offset as shown.



If the CLOSED switch is pressed, the servo position is written into flash memory as servoClosed. The LED will give a long flash while the setting is storted.



Next, open the Shark release and move the servo until the holes are slightly offset as shown.





If the OPEN switch is pressed, the servo position is written into flash memory as servoOpen.



It is important that the holes are slightly offset as shown, to prevent the servo from attempting to force the released aid open or closed.
This will damage the servo.

The M0 will stay in this mode until reset.



As the servo is powered up continuously in Set_Servo mode, the battery will discharge quickly if the device is left in this mode.
Always reset the device to put it back into Cut_Down mode when the servo positions have been stored.

After resetting the device, the shoulder screw can be replaced and the OPEN and CLOSED switches can be used to move the servo.

### Set_Duration:
Set_Duration mode is used to set how long the OPEN or CLOSED switches or pins must be pressed/closed before the servo will move. This is useful since it means
that multiple cut-down devices can be connected together in parallel, using one pair of wires, and triggered consecutively by OPEN pulses of increasing duration.
A 1 second pulse could be used to trigger the first device to release a lift balloon. A 2 second pulse could then be used to trigger a second device to
release the payload from the float balloon.

The code enters Set_Duration mode if the M0 comes out of reset with the MINUS switch held down. Push and hold the MINUS switch, then press and release the RESET switch.
Keep MINUS pressed until the LED has come on and gone out. The device will then enter Set_Duration mode.



intDuration can have a value of 0, 1, 2, 3, 4 or 5 seconds.
The LED will flash intDuration times: 0.2s on, 0.2s off, repeating intDuration times every four seconds.

If the PLUS switch is pressed, intDuration is increased by 1. In the example below, intDuration is set to three.



If the MINUS switch is pressed, intDuration is decreased by 1.

If either OPEN or CLOSED is pressed, intDuration is written into flash memory. The LED will give a long flash while this takes place.

Press reset to put the device back into cut-down mode. In the example below, intDuration has been set to three. On reset, the LED flashes intDuration times.
The OPEN and CLOSED switches now need to be held down for three seconds before the servo moves.



### How do I install the ATSAMD21G18 bootloader?
Get yourself a Segger J-Link programmer and connect it as shown:

Atmel_SAMD21_Programming_Cable

Ignore the RST connection.

Connect the 5V-Supply output from the J-Link to VBUS to power the board while you configure it. Make sure the battery is not connected while you do this.

Follow Lady Ada's excellent instructions:
- https://learn.adafruit.com/proper-step-debugging-atsamd21-arduino-zero-m0/restoring-bootloader

If you are using Atmel's Studio:

Programming_1

Select Tools \ Device Programming

Programming_2

Select J-Link in the Tool pull-down menu
Select ATSAMD21G18A in the Device pull-down menu
Select SWD in the Interface pull-down menu
Then click Apply

Programming_2a

Click the J-Link icon to apply target power to the beacon

Programming_3

Select the Target Power tab and set Current State to Power On. This will apply 5V power from the J-Link
to the beacon VBUS

Programming_4

Close the J-Link window. In the Device Programming window click 'Read' to read the Device Signature and Target Voltage

Programming_5

Click 'Memories', click the '...' icon to select the bootloader Flash file
Click Program to erase, program and verify the device

Programming_6

Finally, select the J-Link icon again, select the Target Power tab and set Current State to Power Off
Close Device Programming and Atmel Studio and you are ready to configure the Beacon with the Arduino code

### How do I upload the Arduino code?
The Cut-Down Device is based on the Adafruit Feather M0 (Adalogger):
- https://www.adafruit.com/products/2796
- https://www.adafruit.com/products/2772

You can follow Lady Ada's excellent instructions:
- https://cdn-learn.adafruit.com/downloads/pdf/adafruit-feather-m0-adalogger.pdf

### What other libraries do I need?
The code uses Cristian Maglie's FlashStorage library to store and retrieve the servo settings:
- https://github.com/cmaglie/FlashStorage

## Acknowledgements

This project wouldn't have been possible without the open source designs and code kindly provided by:
- Adafruit:

   The Adafruit SAMD Board library  
   The design for the Feather M0 Adalogger  
   For more details, check out the product page at:
   - https://www.adafruit.com/product/2772  

   Adafruit invests time and resources providing this open source design, please support Adafruit and open-source hardware by purchasing products from Adafruit!  
   Designed by Adafruit Industries.  
   Creative Commons Attribution, Share-Alike license

- Arduino:

   The Arduino IDE  
   Arduino SAMD Board library  
   RTCZero library

- Cristian Maglie:

   FlashStorage library:
   - https://github.com/cmaglie/FlashStorage

- MartinL:

   M0 PWM tutorial:
   - http://forum.arduino.cc/index.php?topic=346731.msg2610904#msg2610904

## Licence

This project is distributed under a Creative Commons Share-alike 4.0 licence.
Please refer to section 5 of the licence for the "Disclaimer of Warranties and Limitation of Liability".

Enjoy!

**_Paul_**

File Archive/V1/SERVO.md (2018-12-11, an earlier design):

# Servo Modification

The Balloon Cut-Down Device uses a [HiTec HS-82MG servo](https://www.servoshop.co.uk/index.php?pid=HITHS82MG&area=Servo) to operate the
[Scott Archery Shark release aid](https://scottarchery.com/collections/releases/products/shark-release). These servos are lightweight and provide high torque
for their size. But, to allow them to operate reliably at high altitude (low pressure) and low temperature, the standard grease inside the servo needs to be
replaced and lacquer needs to be applied to the internal circuit board.

Servo_1

Servo_2

### Set the Servo to Mid-Range

When you connect the servo to a freshly-programmed cut-down device circuit board, the circuit board will move the servo to its mid-range position.
The servo position is set by a Pulse Width Modulation (PWM) signal on the yellow wire. A pulse width of 1.5msec (1500usec) repeating every 20msec (50Hz)
will set the servo to mid-range. It is important you do this as it will help you relocate the half-moon output gear in the correct position.

You can see how the PWM pulse width causes the servo position to change in the following three images:

- Pulse Width 900usec (0.9msec)

Servo_7

- Pulse Width 1500usec (1.5msec)

Servo_9

- Pulse Width 2100usec (2.1msec)

Servo_8

You can also use the [Serial_Servo](https://github.com/PaulZC/Balloon_Cut-Down_Device/tree/master/Archive/V1/Arduino/Serial_Servo) sketch to position the servo
in the correct position. This code is designed to run on the Cut-Down Device, but it will also work on an Adafruit Feather M0 or M0 Adalogger.
I haven't tested it, but it should work on the Arduino Zero too. Connect: the servo red wire to USB/VBUS (5V);
the servo black wire to GND; the servo yellow (PWM) wire to D5. The Feather must be powered via USB (5V) for reliable servo operation.

### Remove the Screws

Remove the four screws which hold the servo case parts together. You will need a good quality Philips size OO screwdriver
such as the [Wiha PicoFinish 261 P 512](http://uk.farnell.com/wiha/2610040/screwdriver-phillips-no-00x40mm/dp/282303).

Servo_3

Servo_4

### Remove the Standard Grease

Using several [cotton-buds, Q-tips or swabs](https://www.thorlabs.de/thorproduct.cfm?partnumber=CTA10), remove the standard grease from the top part
of the servo housing. Be careful not to leave any cotton strands behind.

Servo_5

Servo_6

Carefully remove the four gears, one at at time, and wipe the grease from each of them using [lint-free lens tissue](https://www.thorlabs.de/thorproduct.cfm?partnumber=MC-5).

Servo_10

### Observe the Output Shaft Position

Once the grease is removed, you will be able to observe the flat on the output shaft. The half-moon output gear has a matching flat to locate it
precisely on the shaft.

Servo_11

### Servo Electronics

Take a look at the servo electronics: PCB with driver IC and push-pull transistors; output shaft position-sensing potentiometer; and DC motor. I do recommend
giving both sides of the driver PCB a coat of lacquer, especially if you are intending to use it at altitude. Cover all of the PCB components with a layer of
[Acrylic Protective Lacquer (conformal coating)](https://uk.rs-online.com/web/p/conformal-coatings/3217324/) between and around the glue HiTec have applied
to the servo wiring. Let the coating dry before you reassemble the servo.

Servo_12

Servo_13

Servo_13a

The servo works by responding to the incoming PWM signal. The motor is driven in one direction or the other by the push-pull driver, until the potentiometer
senses that the output shaft is in the desired position.

### Apply Space Grease

Apply a little Castrol Braycote 601 EF grease to the teeth on all four gears plus the small gear on the motor shaft. Braycote 601 EF is a low temperature (-80C),
low outgassing, non-flammable, non-toxic grease which is approved by NASA. It is expensive, but you are only going to use a very small amount modifying each servo.

Servo_14

### Reassemble

Reassemble the four gears onto the two shafts taking care to match the half-moon output gear with the flat on the output shaft.

Close the case and reinsert the four screws. Do not over-tighten the screws. Label the servo to indicate that the grease has been replaced.

Servo_15

Modifying the servo will of course void your warranty.

This project is distributed under a Creative Commons Attribution + Share-alike (BY-SA) licence.
Please refer to section 5 of the licence for the “Disclaimer of Warranties and Limitation of Liability”.

Enjoy!

**_Paul_**

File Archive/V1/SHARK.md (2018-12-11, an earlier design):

# Shark Release Aid Modification

The Balloon Cut-Down Device uses a [HiTec HS-82MG servo](https://www.servoshop.co.uk/index.php?pid=HITHS82MG&area=Servo) to operate the
[Scott Archery Shark release aid](https://scottarchery.com/collections/releases/products/shark-release). The Shark is a well designed piece
of kit, able to withstand high release loads and yet operate with the minimum of trigger pressure.

Shark_1

Shark_2

### Remove the Wrist Strap

Use a 3/32" hexagon key to remove the 4-40 screw which secures the Shark release to the swivel.

Shark_3

### Versions

The Shark release comes in two versions: one with a removeable trigger and one with a fixed, one-piece trigger. Choose the corresponding
trigger block to match whichever version you have: one replaces the removeable trigger; one slides over the fixed trigger.

Shark_4

### Apply Space Grease

It may be overkill, but I would recommend replacing the standard machine oil in the release with Castrol Braycote 601 EF grease. Braycote 601 EF is a
low temperature (-80C), low outgassing, non-flammable, non-toxic grease which is approved by NASA. It is expensive, but you are only going to need a
very small amount to modify each release.

Shark_5

Working from the side of the release that has the Scott logo (not the word "Shark"), use a 1.6mm parallel pin punch to tap out the pin holding the
jaw nearest the trigger in place.

The two jaws are pushed apart by a spring. Hold them together as you remove the pin, otherwise the spring will disappear into the darkest corner of
your workshop! There is also a ball bearing which makes the jaws move together. Be careful this doesn't also roll away into that same dark corner.

Wipe off the machine oil and then apply Braycote sparingly to all the moving parts.

Re-insert the pin and tap it back into place, working from the side of the release with the word "Shark" on it.

### Add the Trigger Block

[Cut-Down_Device.pdf](https://github.com/PaulZC/Balloon_Cut-Down_Device/blob/master/Archive/V1/Drawings/Cut-Down_Device.pdf) contains the drawings for the two
different versions of the trigger block.

- If your Shark has a green anodised removeable trigger, unscrew it and install the first version of the trigger block using a 3/4" 4-40 UNC screw.
- If your Shark has a black fixed trigger, slide the second version of the trigger block over the trigger using a small amount of epoxy to secure it in place.

Modifying the Shark will of course void your warranty.

This project is distributed under a Creative Commons Attribution + Share-alike (BY-SA) licence.
Please refer to section 5 of the licence for the “Disclaimer of Warranties and Limitation of Liability”.

Enjoy!

**_Paul_**

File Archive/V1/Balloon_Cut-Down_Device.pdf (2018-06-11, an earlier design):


thunderbird\hom e\pclark\D ocum ents\eagle\Balloon_C ut-D ow n\Balloon_C ut-D ow n.sch (Sheet: 1/2)


thunderbird\hom e\pclark\D ocum ents\eagle\Balloon_C ut-D ow n\Balloon_C ut-D ow n.sch (Sheet: 2/2)


24/05/2018 20:38 \\thunderbird\hom e\pclark\D ocum ents\eagle\Balloon_C ut-D ow n\Balloon_C ut-D ow n.brd


Part | X | Y | Angle | Package | Value | Manufacturer | Manufacturer Part No

Farnell
| | | | | | | Part No Mouser Part No | Description
Dimensions 42.55 | 58.42

Fiducials - for solder paste mask alignment:

FD1 | 5.71 | 5.71 | Fiducial 1mm
FD2 | 38.73 | 55.88 | | | | | | Fiducial 1mm

Surface Mount Components:

C1 | 25.65 | 16.51 | 180 0603 | 1uF | Walsin | 0603X105K100CT | 2496916 | MultiLayer Ceramic Capacitor; 1uF; 10V; 0603; X5R
C8 | 17.65 | 23.97 | 0 0603 | 1uF | Walsin | 0603X105K100CT | 2496916 | MultiLayer Ceramic Capacitor; 1uF; 10V; 0603; X5R
C2 | 15.56 | 18.83 | 0 0603 | 12pF | Walsin | 0603N120J500CT | 2496884 | MultiLayer Ceramic Capacitor; 12pF; 50V; 0603
C3 | 15.56 | 21.3 | 0 0603 | 12pF | Walsin | 0603N120J500CT | 2496884 | MultiLayer Ceramic Capacitor; 12pF; 50V; 0603
C4 | 28.7 | 38.35 | 180 0805 | 10µF | Walsin | 0805F106Z100CT | 2496998 | MultiLayer Ceramic Capacitor; 10uF; 10V; 0805
C5 | 26.07 | 28.89 | 180 0805 | 10µF | Walsin | 0805F106Z100CT | 2496998 | MultiLayer Ceramic Capacitor; 10uF; 10V; 0805
C6 | 24.96 | 34.26 | 270 0805 | 10µF | Walsin | 0805F106Z100CT | 2496998 | MultiLayer Ceramic Capacitor; 10uF; 10V; 0805
C9 | 20.16 | 51.24 | 0 0805 | 10µF | Walsin | 0805F106Z100CT | 2496998 | MultiLayer Ceramic Capacitor; 10uF; 10V; 0805
C7 | 22.1 | 34.23 | 270 0805 | 10nF | Walsin | 0805B103K500CT | 2496939 | MultiLayer Ceramic Capacitor; 10nF; 50V; 0805; X7R
C11 | 35.66 | 51.5 | 180 0805 | 10nF | Walsin | 0805B103K500CT | 2496939 | MultiLayer Ceramic Capacitor; 10nF; 50V; 0805; X7R
C13 | 6.35 | 43.82 | 180 0805 | 10nF | Walsin | 0805B103K500CT | 2496939 | MultiLayer Ceramic Capacitor; 10nF; 50V; 0805; X7R
C14 | 6.35 | 52.71 | 180 0805 | 10nF | Walsin | 0805B103K500CT | 2496939 | MultiLayer Ceramic Capacitor; 10nF; 50V; 0805; X7R
C15 | 6.35 | 34.93 | 180 0805 | 10nF | Walsin | 0805B103K500CT | 2496939 | MultiLayer Ceramic Capacitor; 10nF; 50V; 0805; X7R
C16 | 6.35 | 26.04 | 180 0805 | 10nF | Walsin | 0805B103K500CT | 2496939 | MultiLayer Ceramic Capacitor; 10nF; 50V; 0805; X7R
C10 | 18.38 | 46.1 | 90 0805 | 22uF | Murata | GRM219R61A226MEA0D 2611931 | MultiLayer Ceramic Capacitor; 22uF; 10V; X5R; 0805
C12 | 39.34 | 28.8 | 180 0805 | 0.1uF | Walsin | 0805B104K500CT | 2496944 | MultiLayer Ceramic Capacitor; 0.1uF; 50V; 0805; X7R
CON1 | 22.23 | 2.99 | 0 | Micro_USB | Amphenol_FCI | 10103594 | 2293752 | Amphenol FCI 10103594 Micro USB Type B
D1 | 25.53 | 40.67 | 90 SOD-123 | MBR120 | ON SEMICONDUCTOR MBR120VLSFT1G | 1431044 | Schottky Rectifier; 20V; 1A; SOD-123
D2 | 23.56 | 8.99 | 270 SOD-123 | MBR120 | ON SEMICONDUCTOR MBR120VLSFT1G | 1431044 | Schottky Rectifier; 20V; 1A; SOD-123
Q1 | 33.81 | 33.94 | 0 SOT23 | DMG3415U-7 | Diodes Inc. | DMG3415U-7 | 1843688 | MOSFET; P Channel; SOT23-WIDE
R1 | 7.65 | 11.46 | 0 0603 | 2.2K | Panasonic | ERJ3GEYJ222V | 2059610 | Resistor, Thick Film, 2.2K, 75V, 100mW, 0603
R7 | 35.18 | 23.27 | 180 0603 | 2.2K | Panasonic | ERJ3GEYJ222V | 2059610 | Resistor, Thick Film, 2.2K, 75V, 100mW, 0603
R8 | 35.18 | 25.24 | 180 0603 | 2.2K | Panasonic | ERJ3GEYJ222V | 2059610 | Resistor, Thick Film, 2.2K, 75V, 100mW, 0603
R2 | 17.62 | 28.8 | 0 0603 | 330K | Multicomp | MCWR06X3303FTL | 2447338 | Resistor, Thick Film, 330K, 1%, 50V, 100mW, 0603
R3 | 17.62 | 26.73 | 180 0603 | 100K | Multicomp | MC01W08051100K | 9332405 | Chip Resistor; Thick Film; 100k; 150V; 0805; 100mW
R9 | 31.97 | 28.64 | 180 0603 | 100K | Multicomp | MC01W08051100K | 9332405 | Chip Resistor; Thick Film; 100k; 150V; 0805; 100mW
R4 | 26.48 | 45.97 | 270 0805 | 100K_1% | Panasonic | ERJ6ENF1003V | 2303757 | Resistor, Thick Film, 100K, 1% 0.125W, 0805
R5 | 26.48 | 49.97 | 270 0805 | 19K1_0.1% | Panasonic | ERA6ARB1912V | 2094729 | Resistor, Thin Film, 19K1, 0.1%, 0.125W, 0805
R6 | 24.19 | 52.13 | 270 0805 | 68k | Multicomp | MCWR08X6802FTL | 2447706 | Resistor, Thick Film, 68K, 1%, 0.125W
U1 | 29.62 | 14.8 | 270 SOT23-3 | MCP111T-240E/TT | Microchip | MCP111T-240E/TT | 1627192 | Reset Supervisor; SOT23-3; 2.40V; Open Drain; Active Low
U2 | 28.58 | 34.32 | 270 SOT23-5 | SPX3819-3.3 | Exar | SPX3819M5-L-3-3/TR | | 701-SPX3819M5-L-33TR LDO Voltage Regulator; 500mA; SOT-23-5
U3 | 22.23 | 47.16 | 0 QFN-20 | MPM3610 | MPS | MPM3610AGQV-P | | 946-MPM3610AGQV-P Switching Voltage Regulator; 21V; 1.2A; DC/DC
U4 | 33.69 | 45.75 | 180 SOT23-5 | 74AHCT1G125 | Texas Instruments | SN74AHCT1G125DBVR | 1105927 | Buffer / Line Driver; Single Gate
U5 | 26.04 | 22.64 | 90 TQFN48 | ATSAMD21G18_QFN Atmel | ATSAMD21G18A-MF | 2460544 | ATSAMD21G18A-MF; QFN48
X1 | 18.86 | 20.1 | 270 3.2x1.5 | 32.768 | Epson | Q13FC13500004 | 1278036 | Crystal; 32.768kHz; 12.5pF; 3.2 x 1.5mm

Non-surface mount components:

BAT | | | | | Keystone | 1294 | 1650674 | PP3 (9V) Battery Holder Keystone 1294
LED | | | | | Multicomp | 703-0090 | 2112100 | LED, Red, 3mm, 20mA, 1.8V, 643nm
S1 | | | | | Multicomp | MCDTS6-1N | 9471685 | Switch, SPST, 0.05A, 12VDC, 160gf
S2 | | | | | Multicomp | MCDTS6-1N | 9471685 | Switch, SPST, 0.05A, 12VDC, 160gf
S3 | | | | | Multicomp | MCDTS6-1N | 9471685 | Switch, SPST, 0.05A, 12VDC, 160gf
S4 | | | | | Multicomp | MCDTS6-1N | 9471685 | Switch, SPST, 0.05A, 12VDC, 160gf
S5 | | | | | Multicomp | MCDTS6-1N | 9471685 | Switch, SPST, 0.05A, 12VDC, 160gf

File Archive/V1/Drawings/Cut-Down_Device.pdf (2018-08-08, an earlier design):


Scott Archery
Shark
Release Aid

(Left: Fixed Trigger Right: Removable Trigger) 61.2 49.5


12.9

6.5

6.4

9.7

Trigger Block for Removable Trigger Version; M3.0 Tap Thro’ Three Places

Aluminium Plate
Thickness: ¼”

Secured with
McMaster
92196A113
4-40 UNC x ¾” Screw

M3.0 Tap Thro’ Three Places

Trigger Block
for Fixed Trigger Version

Aluminium Plate
Thickness: ¼”

Secured with
Epoxy

Ø4.2 Two Places

Trigger Linkage

Carbon Fibre
Composite
Panel

Thickness: 3mm


HiTec HS-82MG
with
Tower Pro
CH1.0H3G arm
and
McMaster
90323A211
shoulder screw

11.9


PCB and
Battery Holder
(for Energiser
Ultimate Lithium
L522 9V)

Balloon Cut-Down Base Plate; Ø3.0 Three Places; Carbon Fibre Composite Panel Thickness: 3.0mm; Ø3.0 Four Places; Ø2.5 Two Places

Assembled Cut-Down Device; Trigger Block; 4-40 UNC x ¾” Cap Screw; M3 x 4mm Shoulder Screw x 2; Trigger Linkage; HiTec HS-82MG; Tower Pro CH1.0H3G; PCB & 9V Battery; Base Plate; 4-40 UNC x ¼” Cap Screw x 3; M2.5 x 14 Cap Screws and Nylock nuts x 2; M3 x 16 Button Head Screws with 4.5mm OD x 5mm Spacers and Nylock nuts x4

Scott Archery Shark
Release Aid

Cut-Down Device
Mass Estimate
Battery (Energiser L522) | 33.9g
PCB + Battery Holder | 20.6g
Shark Release (No Trigger) | 20.2g
HS-82MG Servo | 19.8g
Base Plate | 17g
M3 x 16 Screws, Nuts, Spacers (4) | 5.8g
Tower Pro Arm | 4.4g
Trigger Block | 2.2g
Trigger Linkage | 2g
M3 x 4 Shoulder Screws (2) | 1.8g
M2.5 x 14 Screws, Nuts (2) | 2.1g
4-40 x ¼” Screws (3) | 1.5g
4-40 x ¾” Screw | 1.0g

Total: 132g

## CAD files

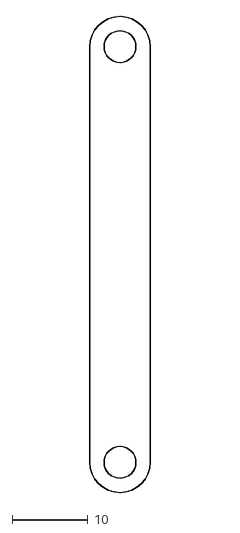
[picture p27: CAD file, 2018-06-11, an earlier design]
Archive/V1/Drawings/Cut-Down_Linkage.dxf
8.00 x 63.0

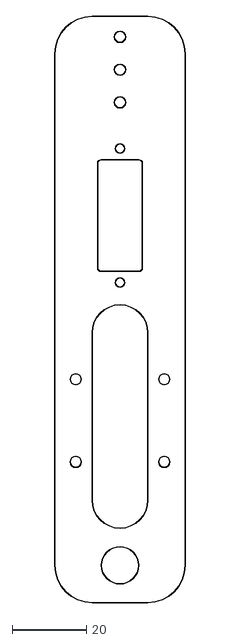
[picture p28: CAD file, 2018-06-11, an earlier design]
Archive/V1/Drawings/Cut-Down_Base.dxf
35.0 x 157.5

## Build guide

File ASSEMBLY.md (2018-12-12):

# Balloon Cut-Down Device Assembly Instructions

Here are the assembly instructions for V3 of the Balloon Cut-Down Device:

### Blank PCB

The [Eagle](https://github.com/PaulZC/Balloon_Cut-Down_Device/tree/master/Eagle) directory contains the schematic and pcb design files.

Start by having the blank PCBs manufactured. If you are based in the UK or Europe, I can recommend
[Multi-CB](https://www.multi-circuit-boards.eu/en/index.html) who can manufacture PCBs in 1-8 working days and
can process the Eagle .brd file direct - there's no need to generate Gerber files.

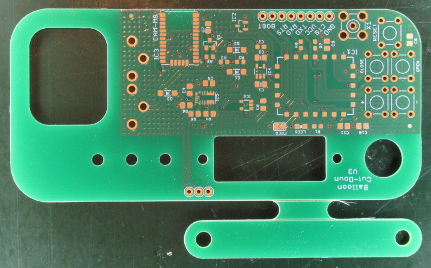
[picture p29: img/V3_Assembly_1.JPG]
V3_Assembly_1


The PCB and trigger linkage are incorporated into a single board. The design includes two score lines which Multi-CB
will machine into the board if you ask them to, allowing the trigger linkage to be easily snapped off.

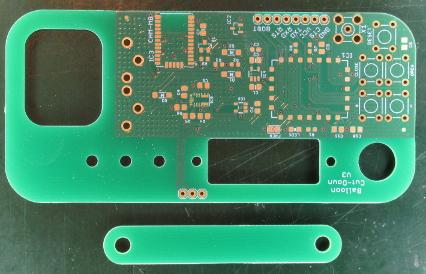
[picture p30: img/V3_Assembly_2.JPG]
V3_Assembly_2


My recommended options are:
- Layers: 2 layers
- Format: Panel
- Panel Type: Multiplier
- Mechanical treatment: Milled and Scored
- Panelization: Yes, by Multi-CB
- Panel size (x/y): 66.04 X 109.22 mm
- Piece size (x/y): 66.04 X 109.22 mm
- PCBs / x-, y-Axis: 1 X 1 Pieces
- Surface finish: Chemical gold (ENIG)
- Material: FR4, 1.55mm
- Cu layers: 35um
- Solder stop: both sides, green
- Marking print: both sides, white
- **Comments: VSCORE data is in layer 148**

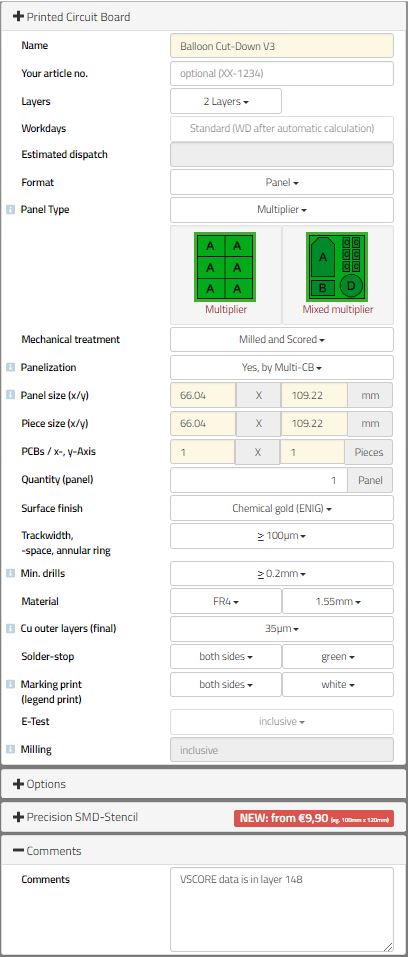
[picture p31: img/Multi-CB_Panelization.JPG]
Multi-CB_Panelization


To allow the cut-down to handle higher loads, you could select 3.2mm FR4 instead of 1.55mm.

### Add solder paste

Multi-CB can also provide you with a solder paste (SMD) stencil for the PCB. You will find the Eagle PCB file for the paste mask in the
[Eagle](https://github.com/PaulZC/Balloon_Cut-Down_Device/tree/master/Eagle) directory. My recommended options are:
- SMD stencil for: top layer
- Size (x/y): 33.02 X 92.71 mm
- Type: custom
- Pad reduction: yes, 10%
- Thickness: 100um
- Existing fiducials: lasered through
- Text type: half lasered
- Double-sided brushing: yes

Secure the blank PCB onto a flat work surface by locating it between two engineer's squares. I use a sheet of toughened glass
as the work surface as it is both very flat and easy to clean.

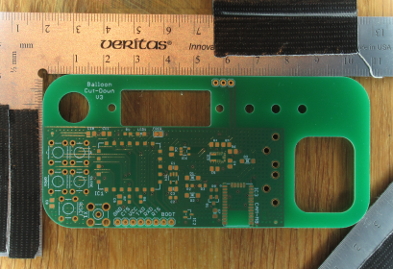
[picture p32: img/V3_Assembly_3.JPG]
V3_Assembly_3


Use the two round fiducials to line up the stencil with the PCB. Secure the stencil with tape.

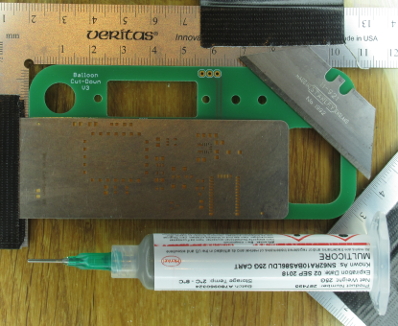
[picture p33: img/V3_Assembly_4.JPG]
V3_Assembly_4


Apply solder paste close to the component cut-outs and then scrape the paste over the stencil using a knife blade
or a similar straight edge. Take appropriate safety precautions when working with solder paste - particularly if you are using
tin-lead solder instead of lead-free.

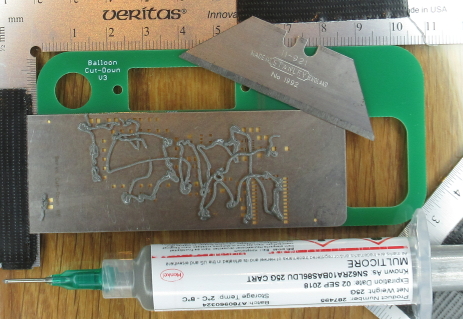
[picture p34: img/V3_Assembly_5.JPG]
V3_Assembly_5


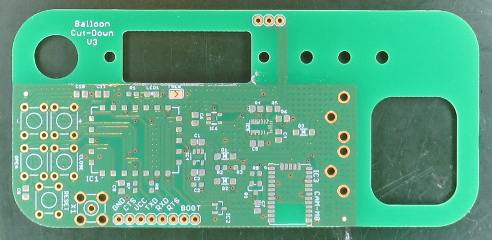
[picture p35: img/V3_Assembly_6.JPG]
V3_Assembly_6


### Position the surface mount components

Position the components onto the blobs of solder paste using tweezers. A magnifier lamp or a USB microscope will
help you place the components in the correct position. IC5 - the 5V regulator - is probably the trickiest
component to position. Take extra time to make sure it is centered accurately on the pads.

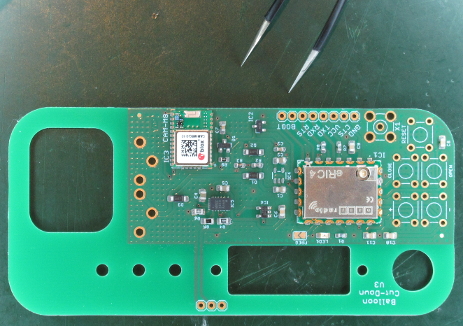
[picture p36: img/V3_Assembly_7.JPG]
V3_Assembly_7


### Reflow the surface mount components

Use a reflow oven to heat the circuit board to the correct temperatures to melt the solder. A reflow oven doesn't need to be
expensive. The one shown below was assembled from:

- Quest 9L 800W mini-oven
- Inkbird PID temperature controller and 40A solid state relay
- Type K thermocouple

Several people have published good reflow oven construction guides, including [this one](http://www.die4laser.com/toaster/index.html).

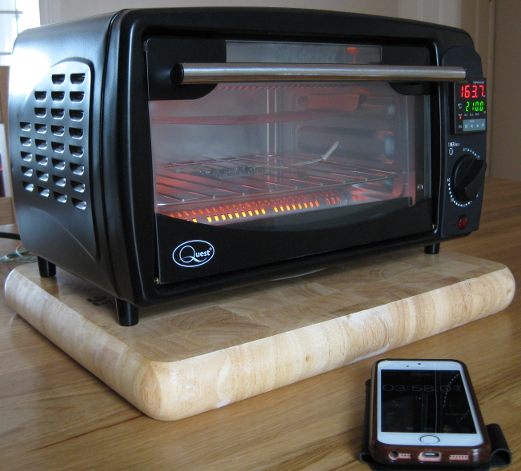
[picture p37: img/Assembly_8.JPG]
Assembly_8


Use the correct temperature profile for your solder paste, but you won't go far wrong with 160C for four minutes, followed by
210C for one minute, followed by a cool-down with the door open. Use a flashlight to check that the solder has melted across
the whole PCB at 210C. Hold the temperature at 210C a little longer if some of the solder paste still appears 'gray' instead of 'silver'.

All being well, your PCB should look like this:

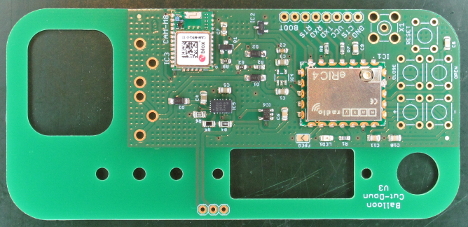
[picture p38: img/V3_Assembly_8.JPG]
V3_Assembly_8


### Check for shorts

Carefully examine all the solder joints and correct any shorts you find.

The 'trick' to removing a short is to add more solder or solder paste and then to use
copper solder braid or wick to remove all the solder in one go.

### Add the non-surface mount components

The non-surface mount components (switches, SMA connector, 3-pin header, battery clips) can now be positioned and soldered by hand.

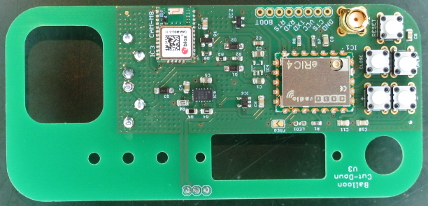
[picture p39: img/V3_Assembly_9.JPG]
V3_Assembly_9


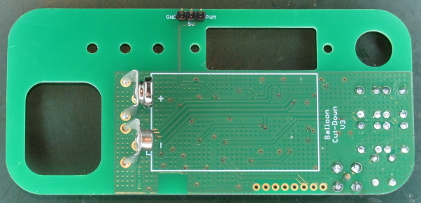
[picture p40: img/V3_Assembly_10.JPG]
V3_Assembly_10


Use a cotton swab dipped in Iso-Propyl Alcohol (IPA / Propanol / rubbing alcohol) to remove any flux residue.

### Mount the Shark Release

Mount the Shark Release using:

- 4-40 UNC x ¼” Socket Head Screw x 3 (McMaster 92196A106)

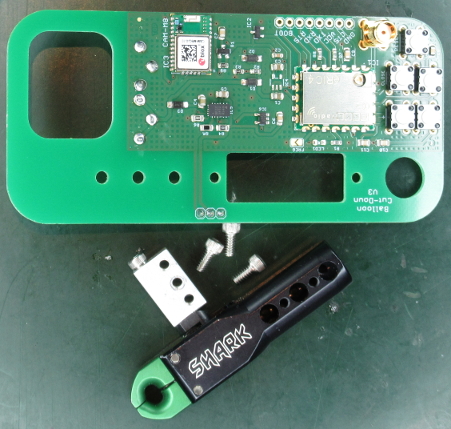
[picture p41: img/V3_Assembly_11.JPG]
V3_Assembly_11


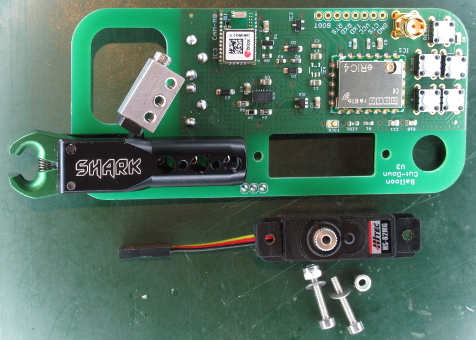
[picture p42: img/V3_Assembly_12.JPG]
V3_Assembly_12


### Mount the Servo

Mount the re-greased servo using:

- M2.5 x 14 Hex Drive Screw x 2 (McMaster 91292A017)
- M2.5 Nylon-Insert Locknut x 2 (McMaster 93625A102)
- M2.5 Washer x 2 (McMaster 90965A115)

**Do not install the servo arm on the servo until the device is in Set_Servo mode and the servo has moved to its mid-range position.**

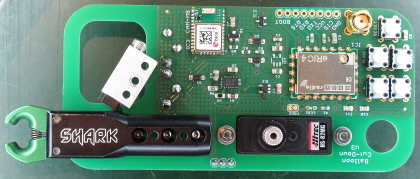
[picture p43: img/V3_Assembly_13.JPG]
V3_Assembly_13


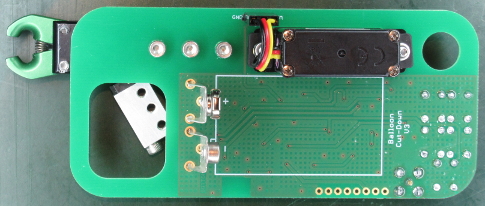
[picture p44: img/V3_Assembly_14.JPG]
V3_Assembly_14


### Configure the eRIC

The eRIC will come pre-programmed with easyRadio V1.5.5. This needs to be replaced with the custom code which you will find in the
[eRIC directory](https://github.com/PaulZC/Balloon_Cut-Down_Device/tree/master/eRIC).

You can find the datasheet for the eRIC on the LPRS website:
- http://www.lprs.co.uk/products/easyradio-ism-modules/eric-soc-rf-modules.html
- http://www.lprs.co.uk/assets/files/eRIC4_9_Datasheet_1.34.pdf

Download and install the latest version of the easyRadio Companion:
- http://www.lprs.co.uk/development-tools/easyradio-evaluation-software.html
- http://www.lprs.co.uk/assets/files/easyRadiosetup%204.1.6.exe

If possible, use an FTDI TTL-232R-3V3 cable to reconfigure the board, although a TTL-232R-5V will work too.
- https://www.ftdichip.com/Products/Cables/USBTTLSerial.htm

Plug the 6-Way connector of the FTDI cable onto one end of an 8-way length of double-height 0.1" header strip. Leave the cable USB connector unconnected for now.

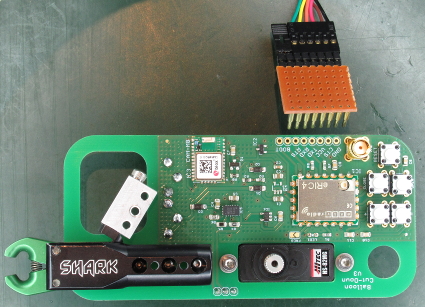
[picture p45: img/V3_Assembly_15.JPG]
V3_Assembly_15


Insert the header strip through the holes in the PCB and then lean the header strip against the side of the holes to ensure good electrical contact. Now plug
the FTDI USB connector into your computer. The LED should be flashing once per second; if it is lit continuously ensure you do not have a jumper link connecting
the two "Boot" pads together. If required, press the Reset button to restart the eRIC.

Start the easyRadio Companion. Registering the software is recommended but is optional. Click on the "eRIC" button. Select the COM port for the FTDI
cable in the UART Settings, then click "Open Port".

Ensure the "Settings" vertical tab is selected.

Click on the "Module Info" horizontal tab. Click on "Discover Module". Wait for all of the module information to be collected. Make a note of the eight digit
eRIC serial number; you will need this to be able to trigger the cut-down. Ideally, print the serial number onto a label and stick it onto the eRIC.

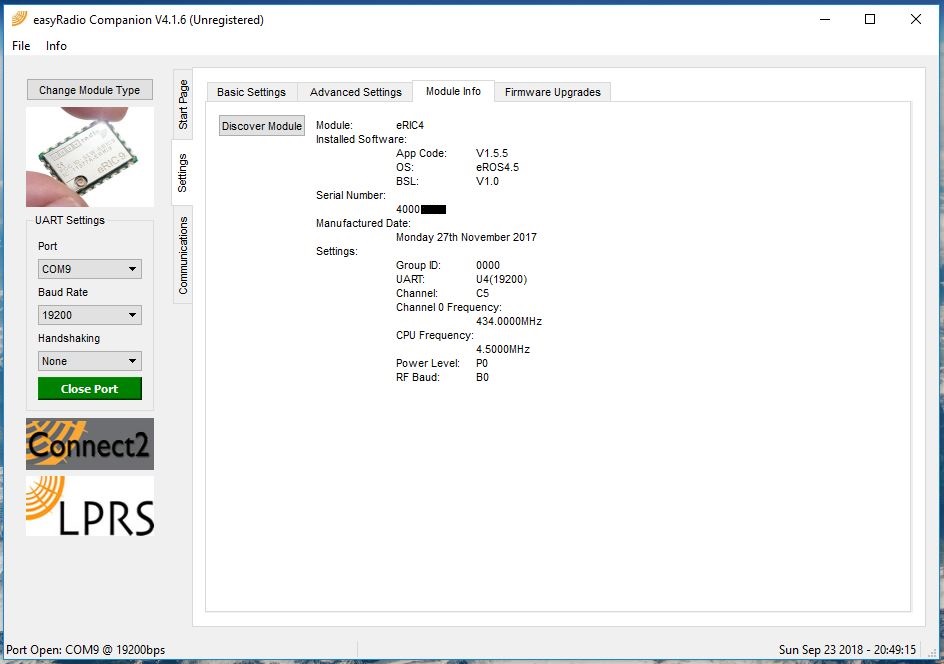
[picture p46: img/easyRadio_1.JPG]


Place a jumper link to link the two "Boot" header pins together; then press the Reset button to place the eRIC into bootloader mode. The LED should light up
continuously. If the LED is still flashing once per second, ensure you have the jumper link installed correctly. If required, press the Reset button to restart
the eRIC.

Click on the "Firmware Upgrades" horizontal tab. Click on "Open Firmware File" and browse to the eRIC4_Servo_CutDown_V3.hex file which you will find in the
[eRIC directory](https://github.com/PaulZC/Balloon_Cut-Down_Device/tree/master/eRIC). Select eRIC9_Servo_CutDown_V3.hex instead if you are using the 868 / 915MHz
eRIC9.

Leave "Enable Code Protect" selected and then click "Upgrade".

All being well, you should see a green progress bar followed by the message "Firmware Update Complete!".

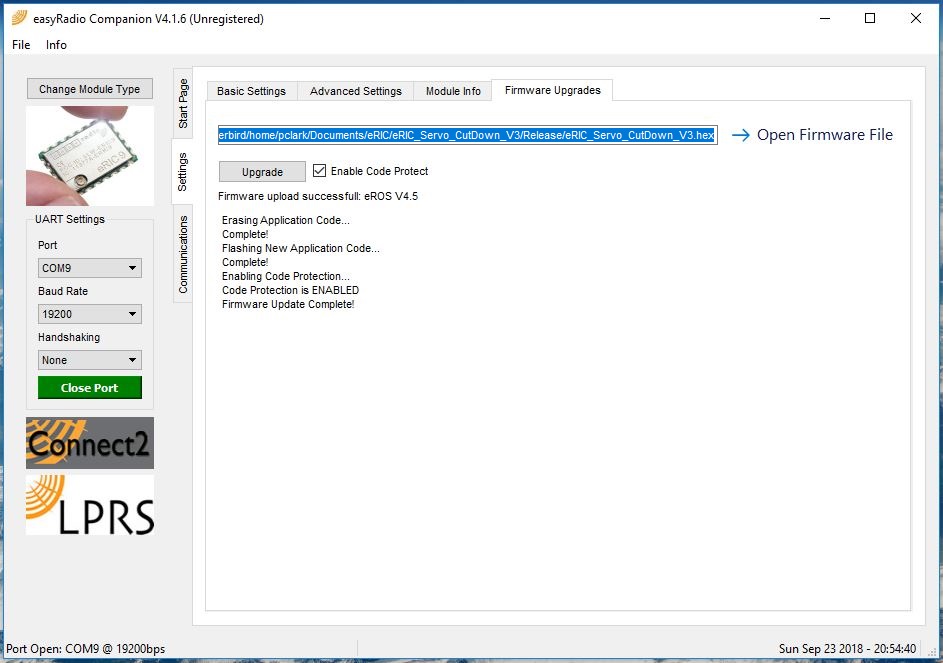
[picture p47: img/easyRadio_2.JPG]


Disconnect the FTDI USB connector from your computer, then remove the header strip.

### Making Changes to the eRIC Code

If you want to alter the programming of the eRIC, you will need to:
- Follow the instructions in http://www.lprs.co.uk/assets/files/Custom%20programming%20eRIC.zip
- Install the Texas Instruments Code Composer Studio
- Copy and unzip the eRIC_Servo_CutDown_V3.zip from the [eRIC directory](https://github.com/PaulZC/Balloon_Cut-Down_Device/tree/master/eRIC) into the Code Composer workspace directory
- Right-click in the Project Explorer window, select "Import" then "CCS Projects"
- Select the folder which you unzipped eRIC_Servo_CutDown_V3 into

You can now make alterations to the code, rebuild the project to produce a new .hex file and then use the easyRadio Companion to programme the eRIC with the new code.

### Lacquer the PCB

I do recommend giving the PCB a coat of lacquer, especially if you are intending to use on a balloon flight.
Cover all of the surface mount components with [Acrylic Protective Lacquer (conformal coating)](https://uk.rs-online.com/web/p/conformal-coatings/3217324/)
taking care to avoid the IO pads and push switches.

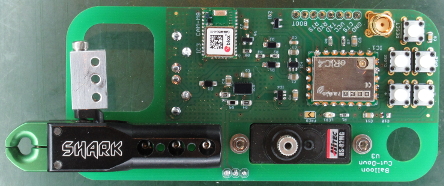
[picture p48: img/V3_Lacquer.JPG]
V3_Lacquer


### Attach The Trigger Linkage

Fix the trigger linkage to the trigger block using:

- M3 x 4mm Dia x 4mm Long Shoulder Screw x 2 (McMaster 90323A211)

**Do not connect the trigger linkage to the servo arm with the second shoulder screw until the servo positions have been set**

### Attach the Battery

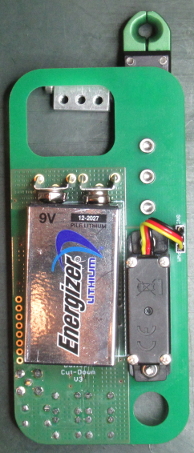
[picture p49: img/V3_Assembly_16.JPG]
V3_Assembly_16


### Move the Servo to Mid-Range

Before attaching the servo arm, move the servo to its mid-range position by putting the cut-down into Set_Servo mode:
- Push and hold the PLUS switch
- Press and release the RESET switch
- Release the PLUS switch

You should hear the servo move to mid-range.

### Disconnect the Battery

### Attach the Servo Arm

Attach the servo arm, securing it with both the socket cap screw and cross-head screw.

### Reattach the Battery

### Set the Servo Positions

Put the cut-down device into Set_Servo mode and set the open and closed servo positions following the instructions
[here](https://github.com/PaulZC/Balloon_Cut-Down_Device/blob/master/CONFIGURE.md#set_servo)

V3_Set_Servo_1

V3_Set_Servo_1a

V3_Set_Servo_2

V3_Set_Servo_2a

### Attach The Trigger Linkage To The Servo

Attach the trigger linkage to the servo arm using the second shoulder screw and your cut-down device is ready to use!

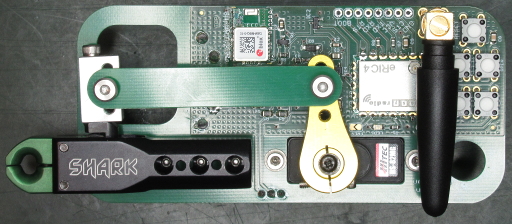
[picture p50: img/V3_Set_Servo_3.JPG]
V3_Set_Servo_3


### The Small Print

This project is distributed under a Creative Commons Attribution + Share-alike (BY-SA) licence.
Please refer to section 5 of the licence for the "Disclaimer of Warranties and Limitation of Liability".

Enjoy!

**_Paul_**

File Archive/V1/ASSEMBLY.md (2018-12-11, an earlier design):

# Balloon Cut-Down Device Assembly Instructions

Here are the assembly instructions for V1 of the Balloon Cut-Down Device:

### Blank PCB

Start by having the blank PCBs manufactured. If you are based in the UK or Europe, I can recommend
[Multi-CB](https://www.multi-circuit-boards.eu/en/index.html) who can manufacture PCBs in 1-8 working days and
can process the Eagle .brd file direct - there's no need to generate Gerber files.

My recommended options are:
- Layers: 2 layers
- Format: single pieces
- Surface finish: chemical gold (ENIG)
- Material: FR4, 1.55mm
- Cu layers: 35um
- Solder stop: both sides, green
- Marking print: both sides, white

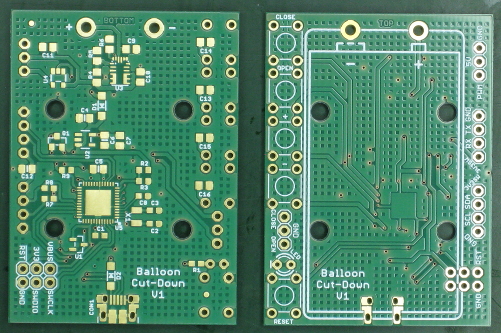
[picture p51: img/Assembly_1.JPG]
Assembly_1


### Add solder paste

Multi-CB can also provide you with a solder paste (SMD) stencil for the PCB. My recommended options are:
- SMD stencil for: **_bottom_** layer
- Make the Y dimension 20mm longer than the PCB itself to allow you to fix it down with tape
- Type: custom
- Pad reduction: yes, 10%
- Thickness: 100um
- Existing fiducials: lasered through
- Text type: half lasered
- Double-sided brushing: yes

Secure the blank PCB onto a flat work surface by locating it between two engineer's squares. I use a sheet of toughened glass
as the work surface as it is both very flat and easy to clean.

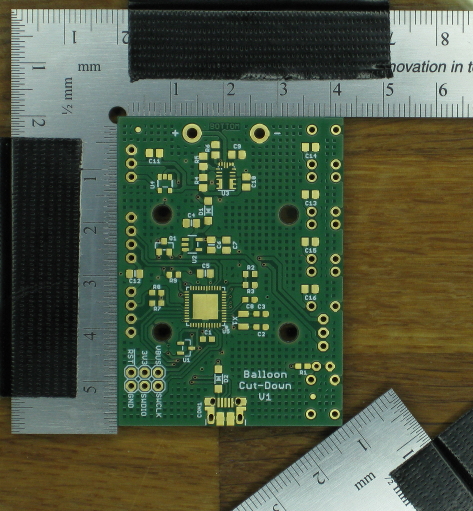
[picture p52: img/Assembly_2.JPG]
Assembly_2


Use the two round fiducials to line up the stencil with the PCB. Secure the stencil with tape.

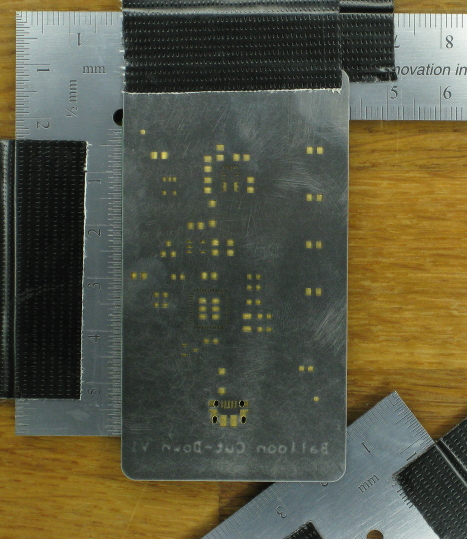
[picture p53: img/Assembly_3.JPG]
Assembly_3


Apply solder paste close to the component cut-outs and then scrape the paste over the stencil using a knife blade
or a similar straight edge. Take appropriate safety precautions when working with solder paste - particularly if you are using
tin-lead solder instead of lead-free.

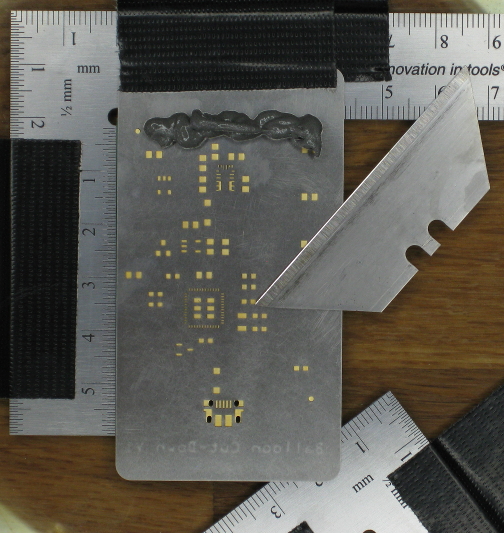
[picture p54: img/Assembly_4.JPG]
Assembly_4


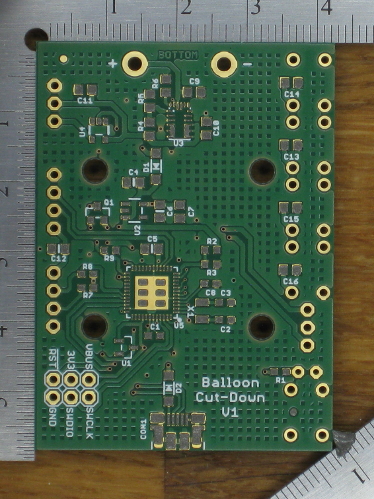
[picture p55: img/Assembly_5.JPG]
Assembly_5


### Position the surface mount components

Position the components onto the blobs of solder paste using tweezers. A magnifier lamp or a USB microscope will
help you place the components in the correct position. U3 - the 5V regulator - is probably the trickiest
component to position. Take extra time to make sure it is centered accurately on the pads.

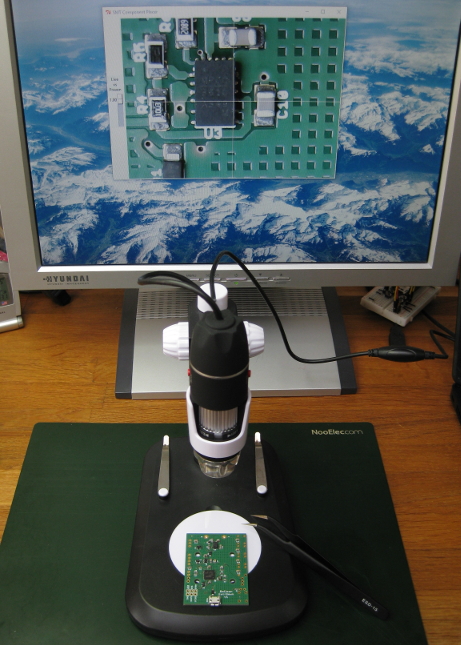
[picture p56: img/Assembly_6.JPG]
Assembly_6


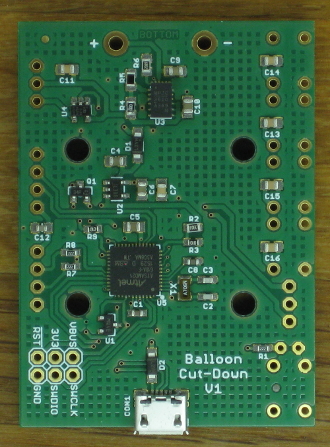
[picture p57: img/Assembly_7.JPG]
Assembly_7


### Reflow the surface mount components

Use a reflow oven to heat the circuit board to the correct temperatures to melt the solder. A reflow oven doesn't need to be
expensive. The one shown below was assembled from:

- Quest 9L 800W mini-oven
- Inkbird PID temperature controller and 40A solid state relay
- Type K thermocouple

Several people have published good reflow oven construction guides, including [this one](http://www.die4laser.com/toaster/index.html).

Assembly_8

Use the correct temperature profile for your solder paste, but you won't go far wrong with 160C for four minutes, followed by
210C for one minute, followed by a cool-down with the door open. Use a flashlight to check that the solder has melted across
the whole PCB at 210C. Hold the temperature at 210C a little longer if some of the solder paste still appears 'gray' instead of 'silver'.

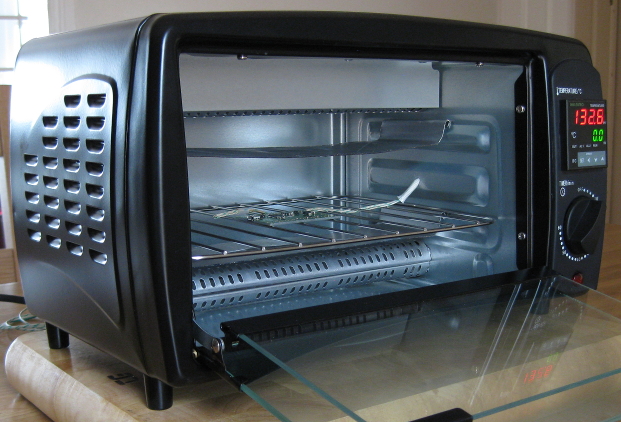
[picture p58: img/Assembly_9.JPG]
Assembly_9


All being well, your PCB should look like this:

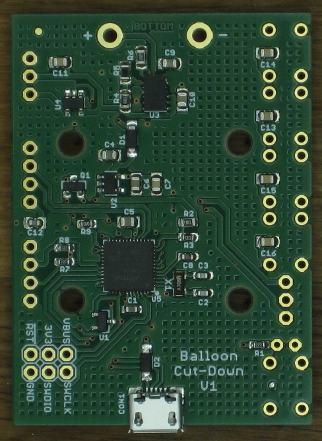
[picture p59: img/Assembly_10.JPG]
Assembly_10


### Check for shorts

Carefully examine all the solder joints and correct any shorts you find.

The 'trick' to removing a short is to add more solder or solder paste and then to use
copper solder braid or wick to remove all the solder in one go.

### Install the bootloader

The SAMD21G18A processor now needs to be configured with a bootloader using a J-Link programmer or similar. See
[How do I install the ATSAMD21G18 Bootloader](https://github.com/PaulZC/Balloon_Cut-Down_Device/blob/master/Archive/V1/LEARN.md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)
for further details.

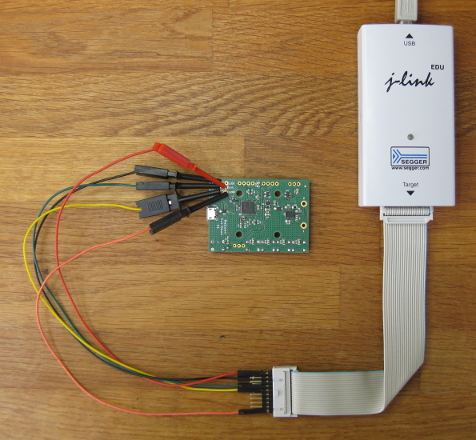
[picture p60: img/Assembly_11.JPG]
Assembly_11


### Add the non-surface mount components

The non-surface mount components (switches, LED, headers, battery clip) can now be positioned on the top of the PCB and soldered by hand.

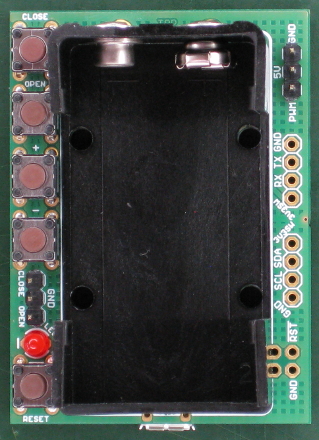
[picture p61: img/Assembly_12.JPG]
Assembly_12


Use a cotton bud (q-tip) dipped in Iso-Propyl Alcohol (IPA / Propanol / rubbing alcohol) to remove any flux residue.

### Lacquer the PCB

I do recommend giving the PCB a coat of lacquer, especially if you are intending to use on a balloon flight.
Cover all of the surface mount components with [Acrylic Protective Lacquer (conformal coating)](https://uk.rs-online.com/web/p/conformal-coatings/3217324/)
taking care to avoid the IO pads.

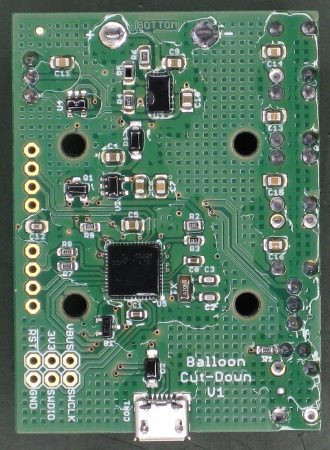
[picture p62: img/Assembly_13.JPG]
Assembly_13


### Test the PCB

The [Arduino](https://github.com/PaulZC/Balloon_Cut-Down_Device/tree/master/Archive/V1/Arduino)
directory contains the Arduino code. Upload it using the Arduino IDE following the instructions
[here](https://github.com/PaulZC/Balloon_Cut-Down_Device/blob/master/Archive/V1/LEARN.md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)

The cut-down device spends most of its time in deep sleep, which means that the Arduino IDE won't recognise it as connected. If you want to reprogram
the board, either:
- press the reset button twice quickly, to put the processor into bootloader mode
or:
- press and hold down the plus or minus switch, the press the reset switch briefly, release the plus or minus switch when the LED goes out. This puts the
board into Set_Servo mode or Set_Duration mode where the processor is powered up continuously.

### Carbon Fibre Parts

The [Drawings](https://github.com/PaulZC/Balloon_Cut-Down_Device/tree/master/Archive/V1/Drawings)
directory contains the drawings for the carbon fibre base plate and trigger linkage. These parts could be made from aluminium or acrylic plastic, but for
use at high altitude I would recommend having them made from 3mm carbon fibre plate.

If you are based in the UK, I can recommend [Carbon Technology Ltd](http://www.carbontechnology.co.uk/) for the manufacture of these parts.

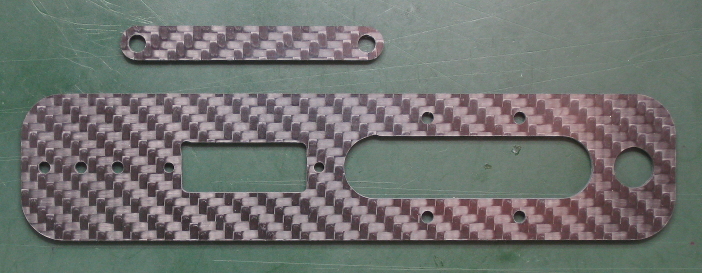
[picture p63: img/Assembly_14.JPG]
Assembly_14


### Mount The PCB

Mount the completed PCB on the base plate using:

- M3 x 16 Hex Drive Screw x 4 (McMaster 92095A184)
- 4.5mm OD, 5mm Long Spacer x 4 (McMaster 94669A099)
- M3 Nylon-Insert Locknut x 4 (McMaster 93625A100)
- M3 Washer x 4 (McMaster 90965A130)

**You will need to file the top off the M3 button head screws to allow the battery to sit correctly in the battery holder.**

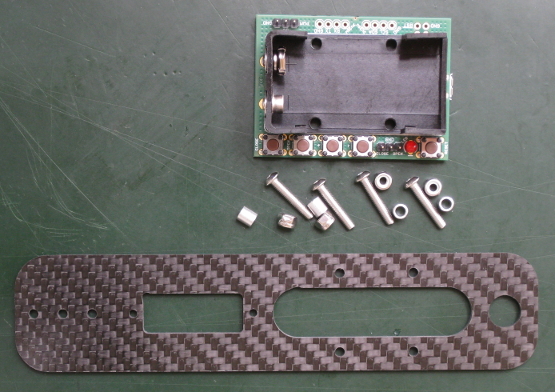
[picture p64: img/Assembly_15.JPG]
Assembly_15


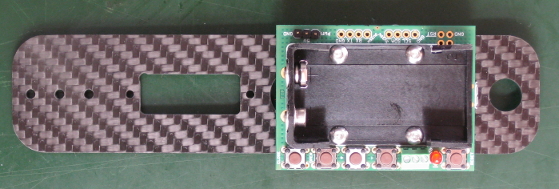
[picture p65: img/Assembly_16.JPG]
Assembly_16


### Mount The Servo

Mount the re-greased servo on the base plate using:

- M2.5 x 14 Hex Drive Screw x 2 (McMaster 91292A017)
- M2.5 Nylon-Insert Locknut x 2 (McMaster 93625A102)
- M2.5 Washer x 2 (McMaster 90965A115)

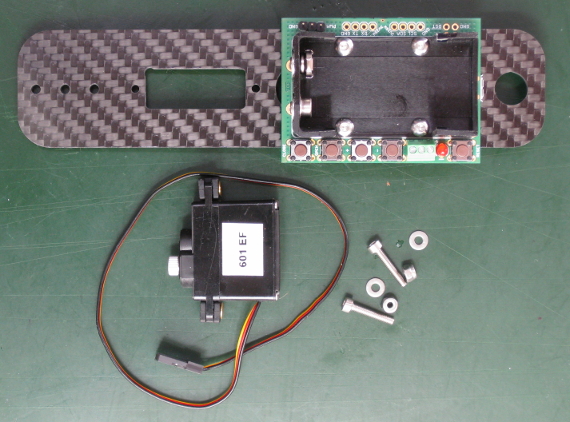
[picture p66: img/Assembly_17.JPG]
Assembly_17


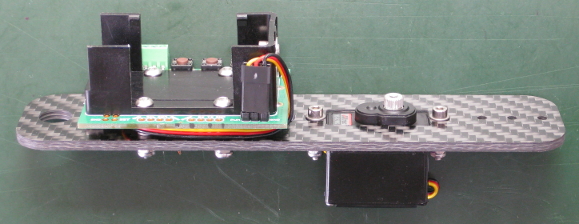
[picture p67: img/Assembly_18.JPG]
Assembly_18


### Mount The Shark Release

Mount the Shark Release on the base plate using:

- 4-40 UNC x ¼” Socket Head Screw x 3 (McMaster 92196A106)

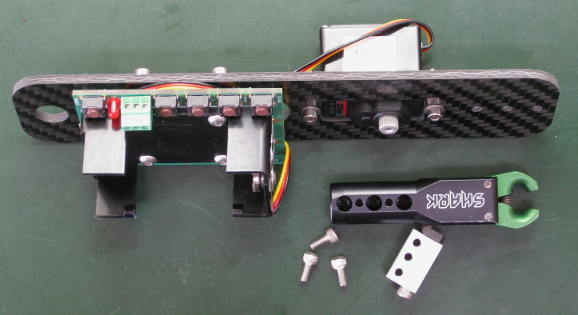
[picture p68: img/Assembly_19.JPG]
Assembly_19


Assembly_20

### Mount The Trigger Linkage

Fix the trigger linkage to the trigger block using:

- M3 x 4mm Dia x 4mm Long Shoulder Screw x 2 (McMaster 90323A211)

**Do not connect the trigger linkage to the servo arm with the second shoulder screw until the servo positions have been set!**

### Set The Servo Positions

Put the cut-down device into Set Servo mode and set the open and closed servo positions following the instructions
[here](https://github.com/PaulZC/Balloon_Cut-Down_Device/blob/master/Archive/V1/LEARN.md#set_servo)

Assembly_21

Assembly_22

Assembly_23

Assembly_24

### Attach The Trigger Linkage To The Servo

Attach the trigger linkage to the servo arm using the second shoulder screw and your cut-down device is ready to use!

Assembly_25

Assembly_26

Assembly_27

Assembly_28

### The Small Print

This project is distributed under a Creative Commons Attribution + Share-alike (BY-SA) licence.
Please refer to section 5 of the licence for the "Disclaimer of Warranties and Limitation of Liability".

Enjoy!

**_Paul_**

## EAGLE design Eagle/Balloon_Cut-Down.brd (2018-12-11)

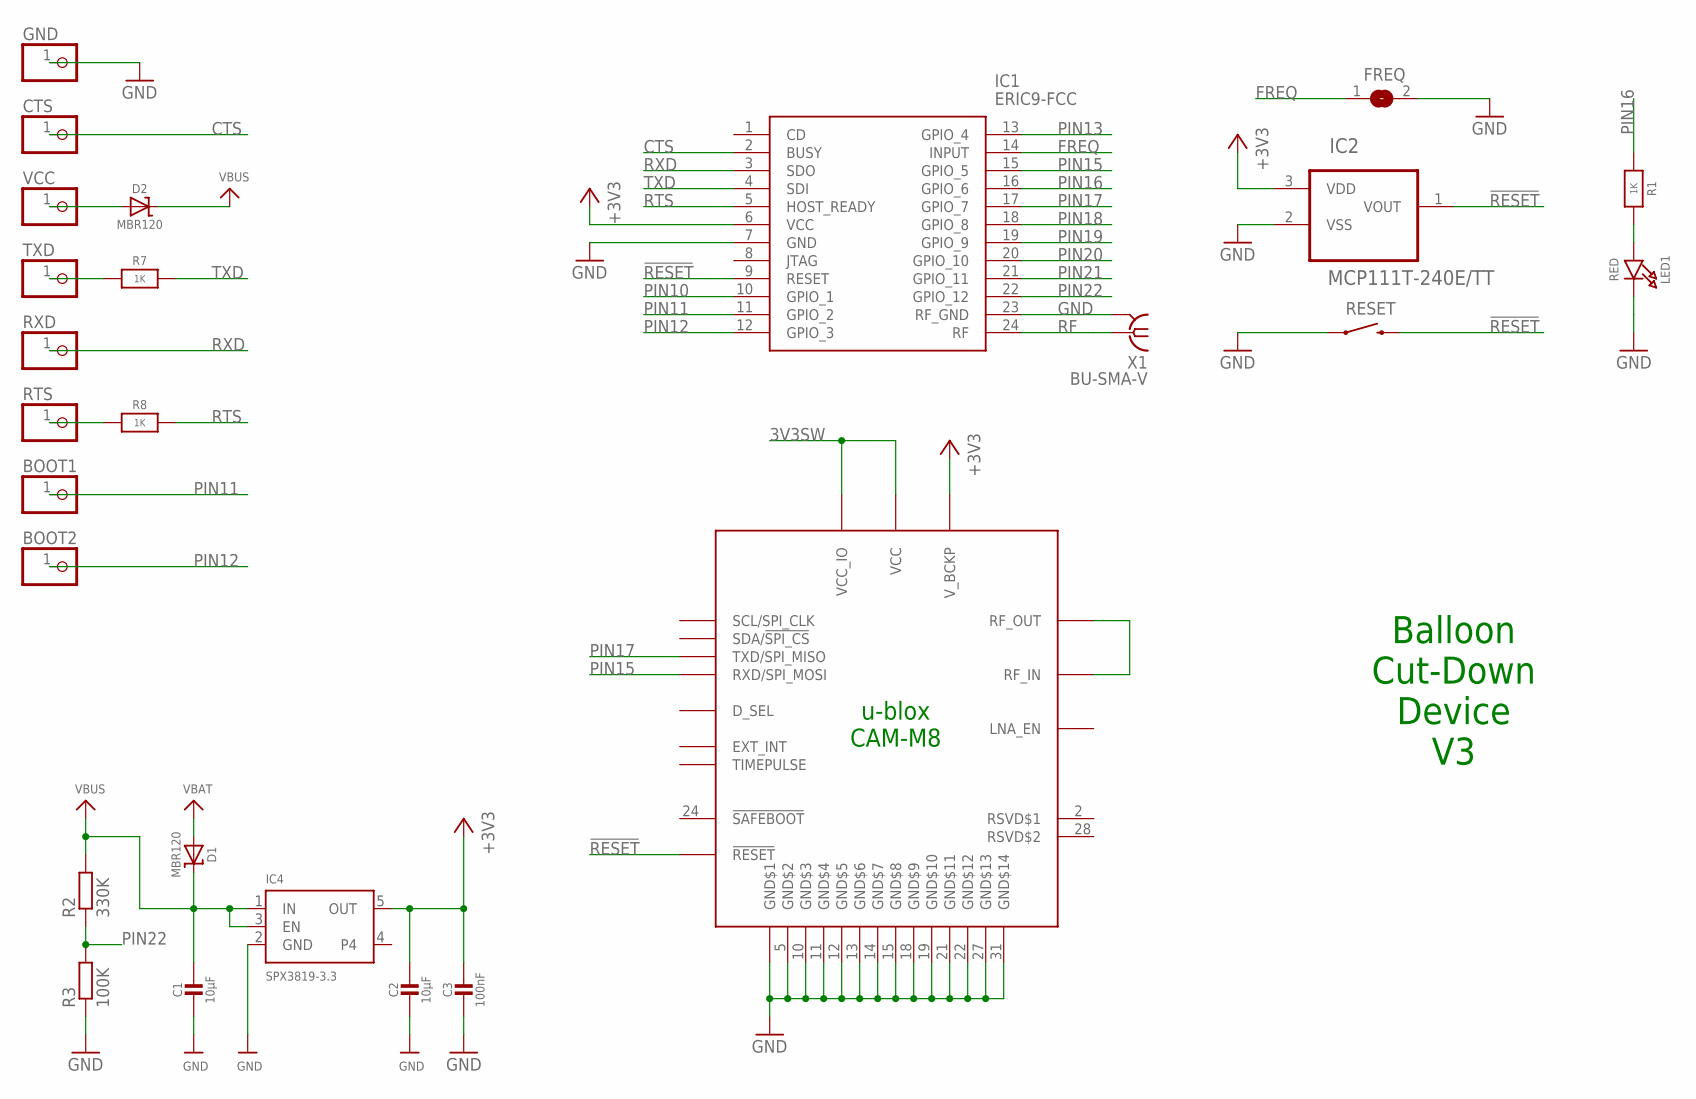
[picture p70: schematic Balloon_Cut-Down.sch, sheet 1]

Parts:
BOOT1, BOOT2: PINHD-1X1; 1X01
C1, C2: 10µF; 0805-NO
C3: 100nF; 0603-NO
CTS: PINHD-1X1; 1X01
D1, D2: MBR120; SOD-123
FREQ: SOLDERJUMPER; SOLDERJUMPER_ARROW_NOPASTE
GND: PINHD-1X1; 1X01
IC1: ERIC9-FCC; ERIC4
IC2: MCP111T-240E/TT; SOT95P237X112-3N; MPN MCP111T-240E/TT
IC3: CAM-M8
IC4: SPX3819-3.3; SOT23-5
LED1: RED; CHIPLED_0805_NOOUTLINE
R1, R7, R8: 1K; 0603-NO
R2: 330K; R0603
R3: 100K; R0603
RESET: SWITCH-MOMENTARY-2PTH; TACTILE-PTH
RTS: PINHD-1X1; 1X01
RXD: PINHD-1X1; 1X01
TXD: PINHD-1X1; 1X01
VCC: PINHD-1X1; 1X01
X1: BU-SMA-V

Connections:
3V3SW: IC3.1 (VCC_IO), IC3.9 (VCC); also elsewhere on the board
!RESET: IC1.9 (RESET), IC2.1 (VOUT), IC3.23 (!RESET), RESET.3 (2)
+3V3: C2.1, C3.1, IC1.6 (VCC), IC2.3 (VDD), IC3.8 (V_BCKP), IC4.5 (OUT); also elsewhere on the board
CTS: CTS.1, IC1.2 (BUSY); also elsewhere on the board
FREQ: FREQ.1, IC1.14 (INPUT)
GND: C1.2, C2.2, C3.2, FREQ.2, GND.1, IC1.7 (GND), IC1.23 (RF_GND), IC2.2 (VSS), IC3.4 (GND$1), IC3.5 (GND$2), IC3.10 (GND$3), IC3.11 (GND$4), IC3.12 (GND$5), IC3.13 (GND$6), IC3.14 (GND$7), IC3.15 (GND$8), IC3.18 (GND$9), IC3.19 (GND$10), IC3.21 (GND$11), IC3.22 (GND$12), IC3.27 (GND$13), IC3.31 (GND$14), IC4.2 (GND), LED1.C, R3.1, RESET.1, X1.2, X1.3 (2), X1.4 (2), X1.5 (2); also elsewhere on the board
unnamed: R7.1, TXD.1
unnamed: IC3.16 (RF_OUT), IC3.17 (RF_IN)
unnamed: LED1.A, R1.2
unnamed: R8.1, RTS.1
unnamed: D2.A, VCC.1
PIN10: IC1.10 (GPIO_1); also elsewhere on the board
PIN11: BOOT1.1, IC1.11 (GPIO_2)
PIN12: BOOT2.1, IC1.12 (GPIO_3)
PIN13: IC1.13 (GPIO_4); also elsewhere on the board
PIN15: IC1.15 (GPIO_5), IC3.26 (RXD/SPI_MOSI)
PIN16: IC1.16 (GPIO_6), R1.1
PIN17: IC1.17 (GPIO_7), IC3.25 (TXD/SPI_MISO)
PIN18: IC1.18 (GPIO_8); also elsewhere on the board
PIN19: IC1.19 (GPIO_9)
PIN20: IC1.20 (GPIO_10)
PIN21: IC1.21 (GPIO_11)
PIN22: IC1.22 (GPIO_12), R2.1, R3.2
RF: IC1.24 (RF), X1.1
RTS: IC1.5 (HOST_READY), R8.2; also elsewhere on the board
RXD: IC1.3 (SDO), RXD.1; also elsewhere on the board
TXD: IC1.4 (SDI), R7.2; also elsewhere on the board
VBAT: D1.A; also elsewhere on the board
VBUS: C1.1, D1.C, D2.C, IC4.1 (IN), IC4.3 (EN), R2.2

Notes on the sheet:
Balloon Cut-Down Device V3
u-blox CAM-M8

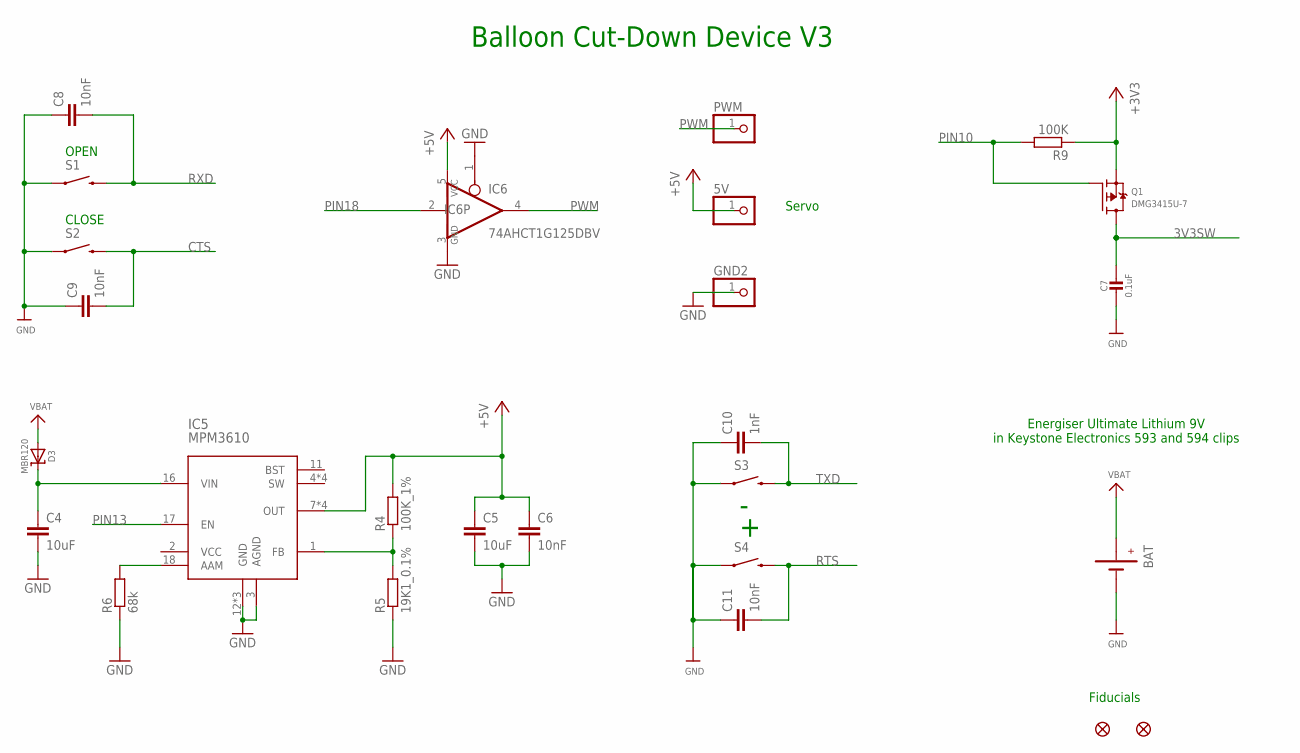
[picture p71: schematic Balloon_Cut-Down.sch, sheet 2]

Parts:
5V: PINHD-1X1; 1X01
BAT: BATTERYBATTERY-9V-KEYSTONE-593-594; BATTERY-9V-KEYSTONE-593-594
C4, C5: 10uF; C0805
C6, C8, C9, C11: 10nF; C0805
C7: 0.1uF; 0805-NO
C10: 1nF; C0805
D3: MBR120; SOD-123
FD1, FD2: FIDUCIAL1X2; FIDUCIAL-1X2
GND2: PINHD-1X1; 1X01
IC5: MPM3610; QFN-20
IC6: 74AHCT1G125DBV; SOT23-5
PWM: PINHD-1X1; 1X01
Q1: DMG3415U-7; SOT23-WIDE
R4: 100K_1%; R0805
R5: 19K1_0.1%; R0805
R6: 68k; R0805
R9: 100K; R0603
S1, S2, S3, S4: SWITCH-MOMENTARY-2PTH; TACTILE-PTH

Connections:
3V3SW: C7.1, Q1.3 (D); also elsewhere on the board
+3V3: Q1.2 (S), R9.1; also elsewhere on the board
+5V: 5V.1, C5.1, C6.1, IC5.7 (OUT), IC5.8 (OUT), IC5.9 (OUT), IC5.20 (OUT), IC6.5 (VCC), R4.2
CTS: C9.2, S2.3 (2); also elsewhere on the board
GND: BAT.GND (-), BAT.GND1 (-), BAT.GND2 (-), C4.2, C5.2, C6.2, C7.2, C8.1, C9.1, C10.1, C11.1, GND2.1, IC5.3 (AGND), IC5.12 (GND), IC5.13 (GND), IC5.14 (GND), IC6.1 (OE), IC6.3 (GND), R5.1, R6.1, S1.1, S2.1, S3.1, S4.1; also elsewhere on the board
unnamed: C4.1, D3.C, IC5.16 (VIN)
unnamed: IC5.1 (FB), R4.1, R5.2
unnamed: IC5.18 (AAM), R6.2
PIN10: Q1.1 (G), R9.2; also elsewhere on the board
PIN13: IC5.17 (EN); also elsewhere on the board
PIN18: IC6.2 (I); also elsewhere on the board
PWM: IC6.4 (O), PWM.1
RTS: C11.2, S4.3 (2); also elsewhere on the board
RXD: C8.2, S1.3 (2); also elsewhere on the board
TXD: C10.2, S3.3 (2); also elsewhere on the board
VBAT: BAT.PWR (+), BAT.PWR1 (+), BAT.PWR2 (+), D3.A; also elsewhere on the board

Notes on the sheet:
Energiser Ultimate Lithium 9V in Keystone Electronics 593 and 594 clips
Balloon Cut-Down Device V3
Fiducials
Servo
OPEN
CLOSE

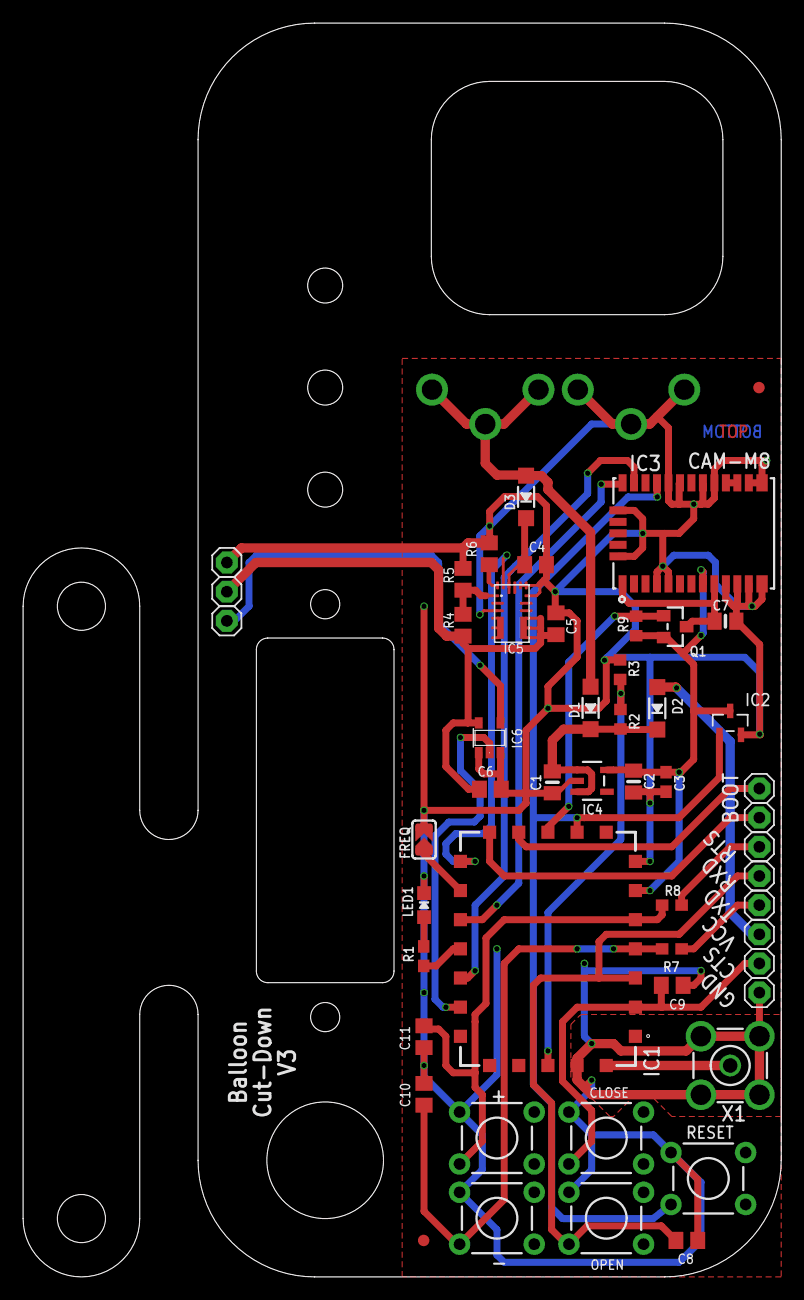
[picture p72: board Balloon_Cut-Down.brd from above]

Board: 2 copper layers, 66.0 x 109.2 mm, 52 parts (1 on the bottom side), 31 nets.

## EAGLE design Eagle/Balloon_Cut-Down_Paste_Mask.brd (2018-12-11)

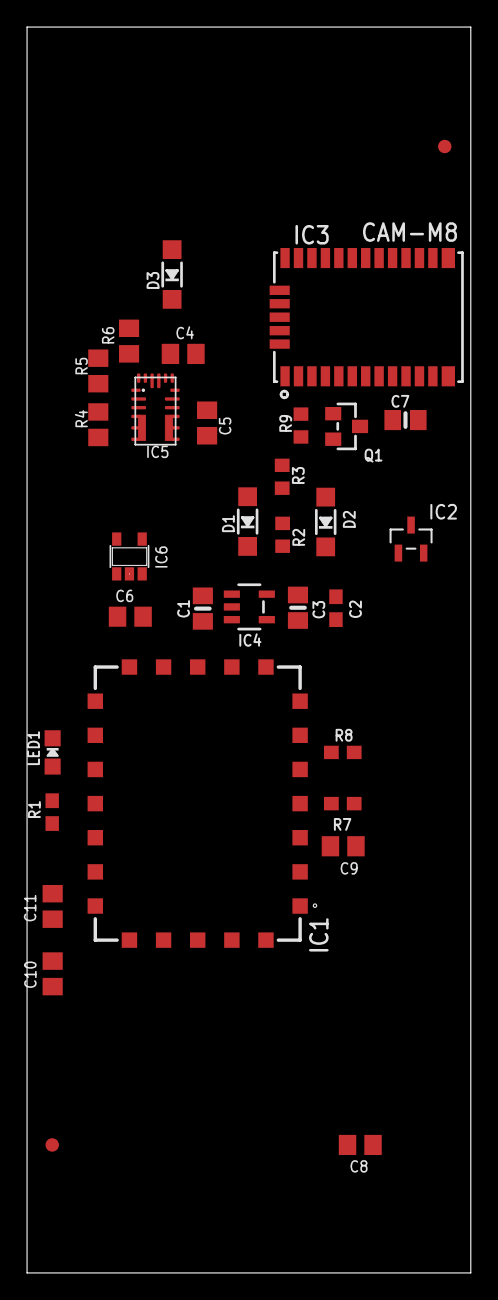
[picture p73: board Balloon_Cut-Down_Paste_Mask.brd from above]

Board: 2 copper layers, 33.0 x 92.7 mm, 33 parts (0 on the bottom side), 2 nets, no tracks yet.

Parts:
C1, C2: 10µF; 0805-NO
C3: 100nF; 0603-NO
C4, C5: 10uF; C0805
C6, C8, C9, C10, C11: 10nF; C0805
C7: 0.1uF; 0805-NO
D1, D2, D3: MBR120; SOD-123
FD1, FD2: FIDUCIAL1X2; FIDUCIAL-1X2
IC1: ERIC9-FCC; ERIC4
IC2: MCP111T-240E/TT; SOT95P237X112-3N
IC3: CAM-M8
IC4: SPX3819-3.3; SOT23-5
IC5: MPM3610; QFN-20
IC6: 74AHCT1G125DBV; SOT23-5
LED1: RED; CHIPLED_0805_NOOUTLINE
Q1: DMG3415U-7; SOT23-WIDE
R1, R7, R8: 1K; 0603-NO
R2: 330K; R0603
R3, R9: 100K; R0603
R4: 100K_1%; R0805
R5: 19K1_0.1%; R0805
R6: 68k; R0805

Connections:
GND: IC4.2, IC6.3
VCC: IC3.9, IC6.5

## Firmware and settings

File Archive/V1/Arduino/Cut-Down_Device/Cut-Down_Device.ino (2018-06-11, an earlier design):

// ###################
// # Cut-Down Device #
// ###################

// A servo-operated cut-down device for high altitude ballooning

// The device operates in three modes:

// Cut_Down:
// The M0 is woken up from deep sleep by an interrupt from the 'Open' or 'Close' switch
// It waits to see if the switch pin stays low for the required amount of time (intDuration) then
// moves the servo to the open or closed position as appropriate.
// By default, intDuration will be zero - i.e. the servo will move immediately.
// The M0 goes back into deep sleep when the servo move is complete.
//
// In reality, the required intDuration is decreased by 0.1 seconds to allow exact whole second key presses
// to trigger the device. E.g. if intDuration is set to '1' a key press of 0.9s or longer will trigger the device.
// This keeps things simpler when triggering the device from an Iridium Beacon via Mobile Terminated messaging.

// Set_Servo:
// If the M0 comes out of reset with the 'Plus' switch held low:
// The servo is moved to its mid-range position (PWM = 1500)
// Depending on whether the 'Plus' or 'Minus' switches are held down, the servo is moved towards
// one limit (PWM = 900) or the other (PWM = 2100)
// If the 'Open' switch is pulled low, the servo position is written into flash memory as servoOpen
// If the 'Closed' switch is pulled low, the servo position is written into flash memory as servoClosed
// The M0 will stay in this mode until reset

// Set_Duration:
// If the M0 comes out of reset with the 'Minus' switch held low:
// The LED will be used to flash the current intDuration
// intDuration can have a value of 0, 1, 2, 3, 4 or 5 seconds
// The LED will flash intDuration times (0.2s on, 0.2s off, repeating intDuration times every four seconds)
// If the 'Plus' switch is pulsed low, intDuration is increased by 1
// If the 'Minus' switch is pulsed low, intDuration is decreased by 1
// If either 'Open' or 'Close' is pulled low, intDuration is written into flash memory
// The M0 will stay in this mode until reset

// This code is intended to be run on Paul's Cut_Down Device:
// https://github.com/PaulZC/Cut-Down_Device

// The Cut-Down_Device PCB is based extensively on the Adafruit Feather M0 (Adalogger)
// https://www.adafruit.com/products/2796
// Set the Arduino Board type to "Adafruit Feather M0"

// With grateful thanks to MartinL: http://forum.arduino.cc/index.php?topic=346731.msg2610904#msg2610904

// Uses Cristian Maglie's FlashStorage library to store the settings in flash memory
// https://github.com/cmaglie/FlashStorage

// With grateful thanks to CaveMoa for his SimpleSleepUSB example
// https://github.com/cavemoa/Feather-M0-Adalogger
// https://github.com/cavemoa/Feather-M0-Adalogger/tree/master/SimpleSleepUSB

// With thanks to Nick Gammon for his ISR code examples:
// http://gammon.com.au/interrupts

// Pin Allocations:
// D15 / A1 / EXTINT8 (Port B Pin 8) = 'Open' switch input (pulled low by the switch)
// D16 / A2 / EXTINT9 (Port B Pin 9) = 'Close' switch input (pulled low by the switch)
// D14 / A0 (Port A Pin 2) = 'Plus' switch input (pulled low by the switch)
// D19 / A5 (Port B Pin 2) = 'Minus' switch input (pulled low by the switch)
// D5 (Port A Pin 15) = PWM signal to the servo
// D8 (Port A Pin 6) = MPM3610 5V Regulator ENable (pull high to enable the regulator and provide power to the servo)
// D9 / A7 (Port A Pin 7) = BUS voltage * 1/4.3 (Used to sense the USB or battery voltage)
// D13 (Port A Pin 17) = Red LED
// D1 (Port A Pin 10) = Serial1 TX : Can be used to connect to an external GPS receiver (RX)
// D0 (Port A Pin 11) = Serial1 RX : Can be used to connect to an external GPS receiver (TX)
// D20 (Port A Pin 22) = SDA : Can be used to connect to an external I2C device e.g. an altitude sensor
// D21 (Port A Pin 23) = SCL : Can be used to connect to an external I2C device e.g. an altitude sensor
// D11 (Port A Pin 16) = 3V3SW Enable : Pull low to provide switched 3V3 power to the 3V3SW pins (for Serial1 and I2C devices)
static const int openSwitch = 15;
static const int closeSwitch = 16;
static const int plusSwitch = 14;
static const int minusSwitch = 19;
const uint8_t pwmPin = 5;
static const int enable5V = 8;
static const int ledPin = 13;
static const int enable3V = 11;
#define VBUS A7 // Point VBUS to A7

// Flash Storage
#include <FlashStorage.h>
typedef struct { // Define a struct to hold the flash variable(s)
  int PREFIX; // Flash storage prefix (0xB5); used to test if flash has been written to before 
  int intDuration; // Minimum Open or Close interrupt duration
  int servoOpen; // Servo PWM value for the open position
  int servoClosed; // Servo PWM value for the closed position
  int CSUM; // Flash storage checksum; the modulo-256 sum of PREFIX and INTERVAL; used to check flash data integrity
} FlashVarsStruct;
FlashStorage(flashVarsMem, FlashVarsStruct); // Reserve memory for the flash variables
FlashVarsStruct flashVars; // Define the global to hold the variables

// Servo Position:
// Min Position = 900
// Mid Position = 1500
// Max Position = 2100
int PWM = 1500;
int servoOpen = 1500;
int servoClosed = 1500;
const int minServo = 900;
const int maxServo = 2100;

int intDuration = 0; // Default required minimum open/close interrupt duration

// Loop Steps
#define Cut_Down      0
#define Set_Servo     1
#define Set_Duration  2
int loop_step = Cut_Down;

volatile bool openSwitch_ISR_flag = false; // Open switch interrupt flag
volatile bool closeSwitch_ISR_flag = false; // Close switch interrupt flag

float vbat = 9.0; // Battery voltage
#define low_bat 6.0 // Low battery voltage

// Read battery voltage, compensating for resistor divider
void get_vbat() {
  vbat = analogRead(VBUS) * (4.3 * 3.3 / 1023.0);
}

void setup()
{
  // initialize digital pins

  pinMode(openSwitch, INPUT_PULLUP);
  pinMode(closeSwitch, INPUT_PULLUP);
  pinMode(plusSwitch, INPUT_PULLUP);
  pinMode(minusSwitch, INPUT_PULLUP);
  pinMode(pwmPin, OUTPUT);
  pinMode(enable5V, OUTPUT);
  digitalWrite(enable5V, LOW); // Disable switched 5V power for servo
  pinMode(ledPin, OUTPUT);
  digitalWrite(ledPin, LOW); // Disable the LED
  pinMode(enable3V, OUTPUT);
  digitalWrite(enable3V, HIGH); // Disable switched 3V power

  int plusSwitchState = digitalRead(plusSwitch); // Read the plus switch state
  int minusSwitchState = digitalRead(minusSwitch); // Read the minus switch state

  if ((plusSwitchState == 1) and (minusSwitchState == 1)) {
    // if both switches are high (not pressed) go into Cut_Down mode
    loop_step = Cut_Down;
  }
  else if ((plusSwitchState == 0) and (minusSwitchState == 1)) {
    // if plusSwitch is low (pressed) go into Set_Servo mode
    loop_step = Set_Servo;
  }
  else if ((plusSwitchState == 1) and (minusSwitchState == 0)) {
    // if minusSwitch is low (pressed) go into Set_Duration mode
    loop_step = Set_Duration;
  }
  else {
    loop_step = Cut_Down; // Default to Cut_Down mode if both switches are pressed
  }
  
  // See if servo settings have already been stored in flash
  // If they have, read them. If not, initialise them.
  flashVars = flashVarsMem.read(); // Read the flash memory
  int csum = flashVars.PREFIX + flashVars.intDuration + flashVars.servoOpen + flashVars.servoClosed; // Sum the prefix and data
  csum = csum & 0xff; // Limit checksum to 8-bits
  if ((flashVars.PREFIX == 0xB5) and (csum == flashVars.CSUM)) { // Check prefix and checksum match
    // Flash data is valid so update BEACON_INTERVAL using the stored value
    intDuration = flashVars.intDuration;
    servoOpen = flashVars.servoOpen;
    servoClosed = flashVars.servoClosed;
  }
  else {
    // Flash data is corrupt or hasn't been initialised so do that now
    flashVars.PREFIX = 0xB5; // Initialise the prefix
    flashVars.intDuration = intDuration; // Initialise the required interrupt duration
    flashVars.servoOpen = servoOpen; // Initialise the servo open position
    flashVars.servoClosed = servoClosed; // Initialise the servo closed position
    csum = flashVars.PREFIX + flashVars.intDuration + flashVars.servoOpen + flashVars.servoClosed; // Initialise the checksum
    csum = csum & 0xff;
    flashVars.CSUM = csum;
    flashVarsMem.write(flashVars); // Write the flash variables
  }

  delay(1000); // Delay to prevent USB recognition problems
  
  // flash red LED intDuration times on reset
  if (intDuration > 0) {
    for (int i=0; i < intDuration; i++) {
      digitalWrite(ledPin, HIGH);
      delay(200);
      digitalWrite(ledPin, LOW);
      delay(200);
    }    
  }

  // Initialise PWM output for servo
  // Output 50Hz PWM on timer TCC0 (14-bit resolution)
  REG_GCLK_GENDIV = GCLK_GENDIV_DIV(3) |          // Divide the 48MHz clock source by divisor 3: 48MHz/3=16MHz
                    GCLK_GENDIV_ID(4);            // Select Generic Clock (GCLK) 4
  while (GCLK->STATUS.bit.SYNCBUSY);              // Wait for synchronization

  REG_GCLK_GENCTRL = GCLK_GENCTRL_IDC |           // Set the duty cycle to 50/50 HIGH/LOW
                     GCLK_GENCTRL_GENEN |         // Enable GCLK4
                     GCLK_GENCTRL_SRC_DFLL48M |   // Set the 48MHz clock source
                     GCLK_GENCTRL_ID(4);          // Select GCLK4
  while (GCLK->STATUS.bit.SYNCBUSY);              // Wait for synchronization

  // Enable the port multiplexer for the PWM channel: timer TCC0 outputs
  PORT->Group[g_APinDescription[pwmPin].ulPort].PINCFG[g_APinDescription[pwmPin].ulPin].bit.PMUXEN = 1;
  // Connect the TCC0 timer to the port outputs - port pins are paired odd PMUO and even PMUXE
  // F & E specify the timers: TCC0, TCC1 and TCC2
  PORT->Group[g_APinDescription[2].ulPort].PMUX[g_APinDescription[2].ulPin >> 1].reg = PORT_PMUX_PMUXO_F | PORT_PMUX_PMUXE_F;
  PORT->Group[g_APinDescription[6].ulPort].PMUX[g_APinDescription[6].ulPin >> 1].reg = PORT_PMUX_PMUXO_F | PORT_PMUX_PMUXE_F;

  // Feed GCLK4 to TCC0 and TCC1
  REG_GCLK_CLKCTRL = GCLK_CLKCTRL_CLKEN |         // Enable GCLK4 to TCC0 and TCC1
                     GCLK_CLKCTRL_GEN_GCLK4 |     // Select GCLK4
                     GCLK_CLKCTRL_ID_TCC0_TCC1;   // Feed GCLK4 to TCC0 and TCC1
  while (GCLK->STATUS.bit.SYNCBUSY);              // Wait for synchronization

  // Dual slope PWM operation: timers countinuously count up to PER register value then down 0
  REG_TCC0_WAVE |= TCC_WAVE_POL(0xF) |         // Reverse the output polarity on all TCC0 outputs
                    TCC_WAVE_WAVEGEN_DSBOTTOM;    // Setup dual slope PWM on TCC0
  while (TCC0->SYNCBUSY.bit.WAVE);               // Wait for synchronization

  // Each timer counts up to a maximum or TOP value set by the PER register,
  // this determines the frequency of the PWM operation:
  // 20000 = 50Hz, 10000 = 100Hz, 2500  = 400Hz
  REG_TCC0_PER = 20000;      // Set the frequency of the PWM on TCC0 to 50Hz
  while(TCC0->SYNCBUSY.bit.PER);

  // The CCBx register value corresponds to the pulsewidth in microseconds (us)
  REG_TCC0_CCB1 = PWM;       // TCC0 CCB1 - center the servo on D5
  while(TCC0->SYNCBUSY.bit.CCB1);

  // Divide the 16MHz signal by 8 giving 2MHz (0.5us) TCC0 timer tick and enable the outputs
  REG_TCC0_CTRLA |= TCC_CTRLA_PRESCALER_DIV8 |    // Divide GCLK4 by 8
                    TCC_CTRLA_ENABLE;             // Enable the TCC0 output
  while (TCC0->SYNCBUSY.bit.ENABLE);              // Wait for synchronization

}

void openSwitch_ISR() // Interrupt service routine for open switch
{
  detachInterrupt(digitalPinToInterrupt(openSwitch)); // Detach the open switch interrupt
  detachInterrupt(digitalPinToInterrupt(closeSwitch)); // Detach the close switch interrupt
  openSwitch_ISR_flag = true;
}

void closeSwitch_ISR() // Interrupt service routine for close switch
{
  detachInterrupt(digitalPinToInterrupt(openSwitch)); // Detach the open switch interrupt
  detachInterrupt(digitalPinToInterrupt(closeSwitch)); // Detach the close switch interrupt
  closeSwitch_ISR_flag = true;
}

void loop() // run over and over again
{
  switch(loop_step) {

    case Cut_Down: {
      noInterrupts(); // Disable interrupts
      
      SCB->SCR |= SCB_SCR_SLEEPDEEP_Msk; // Get ready to put M0 into deep sleep

      // Clear the flags
      openSwitch_ISR_flag = false;
      closeSwitch_ISR_flag = false;

      // Clear any pending interrupts
      REG_EIC_INTFLAG = EIC_INTFLAG_EXTINT8;
      REG_EIC_INTFLAG = EIC_INTFLAG_EXTINT9;

      // (Re)Attach the interrupts
      attachInterrupt(digitalPinToInterrupt(openSwitch), openSwitch_ISR, LOW); // Attach interrupt for open switch
      attachInterrupt(digitalPinToInterrupt(closeSwitch), closeSwitch_ISR, LOW); // Attach interrupt for close switch
      
      interrupts(); // Re-enable interrupts
      
      // Put M0 into Deep Sleep
      __WFI();

      // Wake-up

      unsigned long wake_millis = millis(); // Record the wake-up time

      // Turn on LED to indicate wake-up
      digitalWrite(ledPin, HIGH);

      int switchReleased = 0; // flag to indicate if switch has been released
      
      // calculate the maximum wait time in millis depending on value of intDuration
      // if intDuration is non-zero, max_wait_millis is decreased by 0.1 seconds so that it will respond correctly to intDurations of whole seconds
      unsigned long max_wait_millis;
      if (intDuration > 0) {
        max_wait_millis = (((unsigned long)intDuration) * 1000UL) - 100UL;
      }
      else {
        max_wait_millis = 0;
      }

      if (openSwitch_ISR_flag == true) {
        // If the open switch caused the interrupt
        // Check to see if the switch is held longer than max_wait_millis
        while ((switchReleased == 0) && ((millis() - wake_millis) < max_wait_millis)) {
          switchReleased = digitalRead(openSwitch);
          delay(1); // Avoid too many calls to millis() as it suspends interrupts
        }
      }
      else {
        // If the close switch caused the interrupt
        // Check to see if the switch is held longer than max_wait_millis
        while ((switchReleased == 0) && ((millis() - wake_millis) < max_wait_millis)) {
          switchReleased = digitalRead(closeSwitch);
          delay(1); // Avoid too many calls to millis() as it suspends interrupts
        }        
      }

      // Either the switch has been released or max_wait_millis has been reached
      if ((switchReleased == 0) && ((millis() - wake_millis) >= max_wait_millis)) {
        // If the switch is still pressed and max_wait_millis has been reached, move the servo
        
        // Change the servo PWM
        if (openSwitch_ISR_flag == true) {
          PWM = servoOpen;
        }
        else {
          PWM = servoClosed;
        }
        REG_TCC0_CCB1 = PWM; // TCC0 CCB1 - change the servo PWM on D5
        while(TCC0->SYNCBUSY.bit.CCB1);

        // Power up the servo
        digitalWrite(enable5V, HIGH);
        
        // Wait 2 seconds (blocking!!) - flash LED if battery is low
        for (int i=0; i < 10; i++) {
          get_vbat(); // Read battery voltage
          digitalWrite(ledPin, HIGH);
          delay(100);
          if (vbat < low_bat) {
            digitalWrite(ledPin, LOW);
          }
          delay(100);
        }
        
        // Power down the servo
        digitalWrite(enable5V, LOW);
      }

      // Turn off the LED
      digitalWrite(ledPin, LOW);

    }
    break;
    
    case Set_Servo: {

      // Power up the servo
      digitalWrite(enable5V, HIGH);      

      bool decOne = false; // Flag to indicate that the PWM should be decremented by one
      bool incOne = false; // Flag to indicate that the PWM should be incremented by one

      int plusSwitchState = digitalRead(plusSwitch); // Read the plus switch state
      int minusSwitchState = digitalRead(minusSwitch); // Read the minus switch state
    
      if ((plusSwitchState == 0) and (minusSwitchState == 1)) {
        // If only the plusSwitch is low (pressed) decrement the PWM value
        decOne = true;
      }
      else if ((plusSwitchState == 1) and (minusSwitchState == 0)) {
        // If only the minusSwitch is low (pressed) increment the PWM value
        incOne = true;
      }
      // If neither or both switches are pressed, do nothing
      
      if ((incOne == true) || (decOne == true)) {
        // If either switch was pressed
        if (incOne == true) {
          if (PWM < maxServo) {
            PWM = PWM + 1;
          }
        }
        else {
          if (PWM > minServo) {
            PWM = PWM - 1;
          }
        }
      }

      // Update the servo PWM
      REG_TCC0_CCB1 = PWM; // TCC0 CCB1 - change the servo PWM on D5
      while(TCC0->SYNCBUSY.bit.CCB1);

      // Wait (blocking!!)
      delay(10);
        
      bool updateFlash = false; // Flag to indicate that the flash storage should be updated

      int openSwitchState = digitalRead(openSwitch); // Read the open switch state
      int closeSwitchState = digitalRead(closeSwitch); // Read the close switch state
    
      if ((openSwitchState == 0) and (closeSwitchState == 1)) {
        // If only the openSwitch is low (pressed) update servoOpen
        updateFlash = true;
        servoOpen = PWM;
      }
      else if ((openSwitchState == 1) and (closeSwitchState == 0)) {
        // If only the closeSwitch is low (pressed) update servoClose
        updateFlash = true;
        servoClosed = PWM;
      }
      // If neither or both switches are pressed, do nothing
        
      if (updateFlash == true) {
        // If either switch was pressed, update flash memory
        flashVars.PREFIX = 0xB5; // Reset the prefix (hopefully redundant!)
        flashVars.intDuration = intDuration; // Store the required interrupt duration
        flashVars.servoOpen = servoOpen; // Store the servo open position
        flashVars.servoClosed = servoClosed; // Store the servo closed position
        int csum = flashVars.PREFIX + flashVars.intDuration + flashVars.servoOpen + flashVars.servoClosed; // Update the checksum
        csum = csum & 0xff;
        flashVars.CSUM = csum;
        flashVarsMem.write(flashVars); // Write the flash variables
        
        digitalWrite(ledPin, HIGH); // Turn on the LED
        delay(2000); // Wait (blocking!)
        digitalWrite(ledPin, LOW); // Turn off the LED
        delay(2000); // Wait (blocking!)
        
        // Wait until both open and close switches have been released
        while ((openSwitchState == 0) || (openSwitchState == 0)) {
          openSwitchState = digitalRead(openSwitch); // Read the open switch state
          closeSwitchState = digitalRead(closeSwitch); // Read the close switch state
        }
      }
      
    }
    break;
    
    case Set_Duration: {
      // Read millis
      unsigned long millis_now;
      millis_now = millis();

      int double_secs;
      double_secs = (int)(millis_now / 2000UL); // Divide millis by 2000 to get double-seconds
      int hecto_millis;
      hecto_millis = (int)(millis_now - ((unsigned long)(double_secs * 2000))); // Remove double-seconds to leave hecto_millis containing 0-1999 milliseconds
      hecto_millis = hecto_millis / 100; // Divide by 100 to leave hecto_millis in the range 0-19

      if ((double_secs % 2) == 0) { // If double_secs is even
        if ((hecto_millis % 4) < 2) { // If hecto_millis is 0,1,4,5,8,9 etc...
          if (intDuration > 0) { // If intDuration is non-zero
            if ((hecto_millis / 4) < intDuration) {
              // If hecto_millis divided by four is greater than or equal to intDuration, turn on the LED
              digitalWrite(ledPin, HIGH); // Turn on the LED
            }
            else {
              digitalWrite(ledPin, LOW); // Turn off the LED
            }
          }
          else {
            digitalWrite(ledPin, LOW); // Turn off the LED
          }
        }
        else {
          digitalWrite(ledPin, LOW); // Turn off the LED
        }
      }
      // If secs is even, turn the LED off
      else {
        digitalWrite(ledPin, LOW); // Turn off the LED
      }

      int plusSwitchState = digitalRead(plusSwitch); // Read the plus switch state
      int minusSwitchState = digitalRead(minusSwitch); // Read the minus switch state

      if ((plusSwitchState == 0) || (minusSwitchState == 0)) {
        // If either the plus switch or the minus switch is pressed
        if ((plusSwitchState == 0) and (minusSwitchState == 1)) {
          // If only the plusSwitch is low (pressed) increment intDuration
          if (intDuration < 5) {
            intDuration = intDuration + 1;
          }
        }
        else if ((plusSwitchState == 1) and (minusSwitchState == 0)) {
          // If only the minusSwitch is low (pressed) decrement intDuration
          if (intDuration > 0) {
            intDuration = intDuration - 1;
          }
        }
        // If neither or both switches are pressed, do nothing

        while ((plusSwitchState == 0) || (minusSwitchState == 0)) {
          // Wait for both switches to be released
          delay(10); // Switch debounce
          plusSwitchState = digitalRead(plusSwitch); // Read the plus switch state
          minusSwitchState = digitalRead(minusSwitch); // Read the minus switch state          
        }
      }
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

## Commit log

2018-06-11 Major update
    [Balloon_Cut-Down.brd, Balloon_Cut-Down.sch, Cut-Down_Base.dxf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]
2018-06-23 Updated the wiring diagram
2018-12-11 Major update for the V3 PCB
    Major update for the V3 PCB: the cut-down is now based on the eRIC4 or eRIC9 radio controller and can be triggered by radio; a u-blox CAM-M8Q provides altitude information; the Shark and Servo are no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
    [Balloon_Cut-Down.brd, Balloon_Cut-Down.sch, Balloon_Cut-Down_Paste_Mask.brd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]

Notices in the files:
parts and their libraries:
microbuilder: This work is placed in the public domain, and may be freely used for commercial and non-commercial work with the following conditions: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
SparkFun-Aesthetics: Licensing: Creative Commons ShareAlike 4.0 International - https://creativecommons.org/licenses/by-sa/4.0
